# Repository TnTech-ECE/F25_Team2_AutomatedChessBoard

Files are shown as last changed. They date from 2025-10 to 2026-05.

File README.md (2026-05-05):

# Chess 2 Impress

## Executive Summary

Smart chessboards enhance the over-the-board chess experience through automated piece movement and AI opponent integration. Existing commercial options, however, cost hundreds to thousands of dollars (putting them out of reach for most players). Chess 2 Impress is a low-cost, accessible, **voice-controlled** chessboard (built for under $660 in materials). Players speak their moves using natural chess notation, and the board physically moves the pieces (using a CoreXY gantry with an under-board electromagnet). The system supports single-player games against the Stockfish chess engine, two-player games, and includes automated capture handling and board reset. Voice recognition runs locally on a Raspberry Pi (using the Vosk engine), requiring no internet connection. An LCD display provides real-time game feedback, and a battery-backed UPS allows over 2 hours of portable gameplay. The project demonstrates that a fully functional automated chess board can be built with off-the-shelf components (at less than commercial prices), while maintaining accessibility for players with limited mobility or visual impairments.

## Capabilities

- **Voice-controlled gameplay** using the Vosk speech recognition engine, supporting algebraic notation and common variations (e.g., "move knight a six," "move c2c4," "move castle"). There was a 97% first-try recognition accuracy across multiple speakers.
- **Automated piece movement** via a CoreXY gantry system driven by two NEMA 17 stepper motors and TMC2209 drivers, with an under-board electromagnet for contactless piece manipulation.
- **Edge-lane pathing algorithm** that routes pieces along square boundaries during movement, avoiding collisions with adjacent pieces on the board.
- **AI opponent integration** using the Stockfish chess engine for single-player games, with full move validation (through python-chess). This ensures 100% correct legal/illegal move classification.
- **Capture and reset handling** where captured pieces are automatically moved to dedicated discard rows, and the board resets all pieces to starting positions at the end of a game.
- **Binary UART communication** between the Raspberry Pi (processing) and Arduino Nano (motion control), with a handshake protocol that rejects boot noise and ensures reliable command transfer.
- **Battery-powered portable operation** via a DFRobot UPS HAT with 4×18650 cells, delivering over 2 hours of continuous gameplay (with seamless switchover from wall power).
- **LCD display feedback** showing move confirmations, illegal move alerts, game status, and system messages within approximately 1 second of voice input.
- **Fault protection** including TMC2209 DIAG pin monitoring, MOSFET flyback diode clamping, software position clamping (to prevent rail collisions), and EEPROM position saving.

## Salient Outcomes

- **Voice recognition exceeded expectations**: achieving 97% first-try recognition and 95% correctness (across 5 speakers with varied accents). This was well above the 80% specification.
- **The edge-lane pathing algorithm** was one of the most complex and iterative parts of the firmware development. Pieces must travel along square edges (never through intermediate square centres) to avoid displacing adjacent pieces. The final algorithm handles straight, diagonal, knight, and arbitrary L-shaped moves (for captures and discards) using a unified exit-edge / entry-edge framework.
- **Electromagnet switching latency measured at 3 microseconds**: over 3,300 times faster than the 10ms specification, demonstrating that the MOSFET circuit adds essentially zero delay to the move-completion budget.
- **The blown fuse debugging saga** taught the team that hardware failures can mimic software bugs. Multiple debugging sessions chasing "wrong direction" firmware issues were ultimately caused by a single blown fuse disabling one stepper motor, producing diagonal movement instead of the intended axis-aligned motion.
- **Move completion time remains the primary unmet specification**: Even the shortest possible move takes over 5 seconds with current firmware settings, and worst-case moves approach 30 seconds. Increasing stepper speed and acceleration in firmware is the straightforward fix, but could not be implemented without drastic redesigns to the electromagnet and acryllic setup.

## Project Demonstration & Images

**Demo Video:** (click the thumbnail below) Watch the video (https://youtu.be/9_9py33vPpE?si=CPKPgexxfqgLKRPD)

**Project Images:**

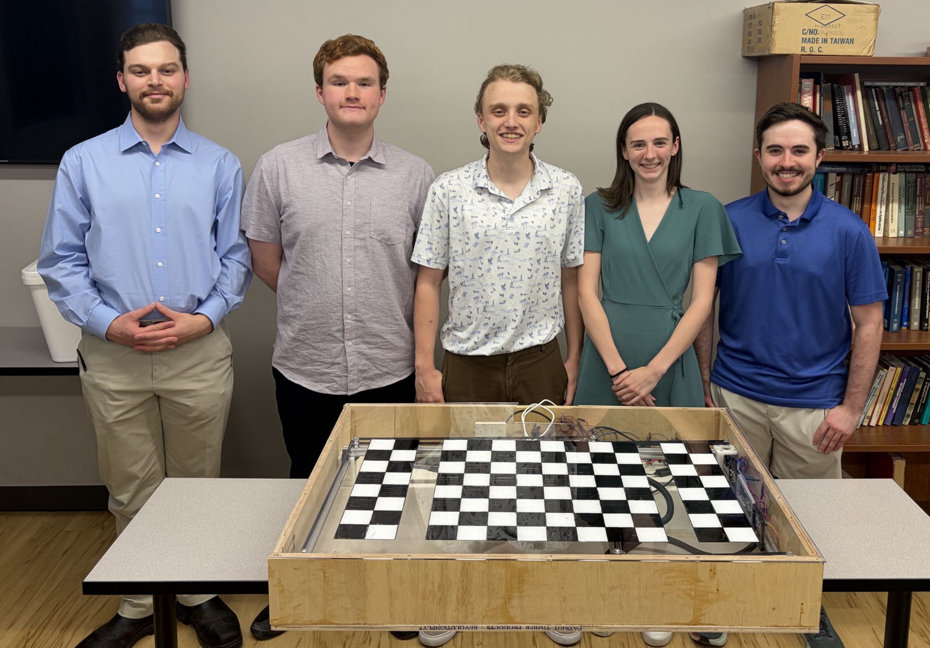
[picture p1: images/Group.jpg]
Group Photo


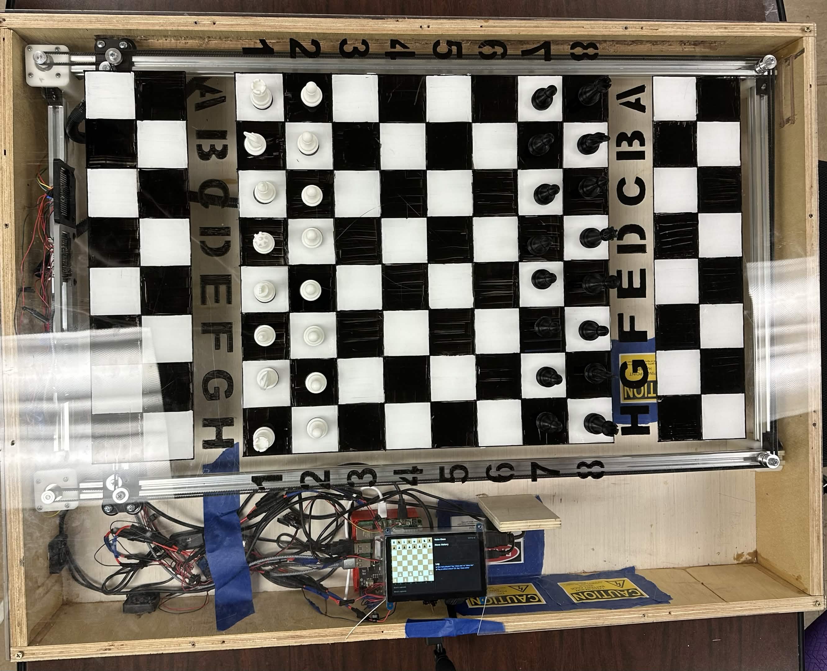
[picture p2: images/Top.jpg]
Top View


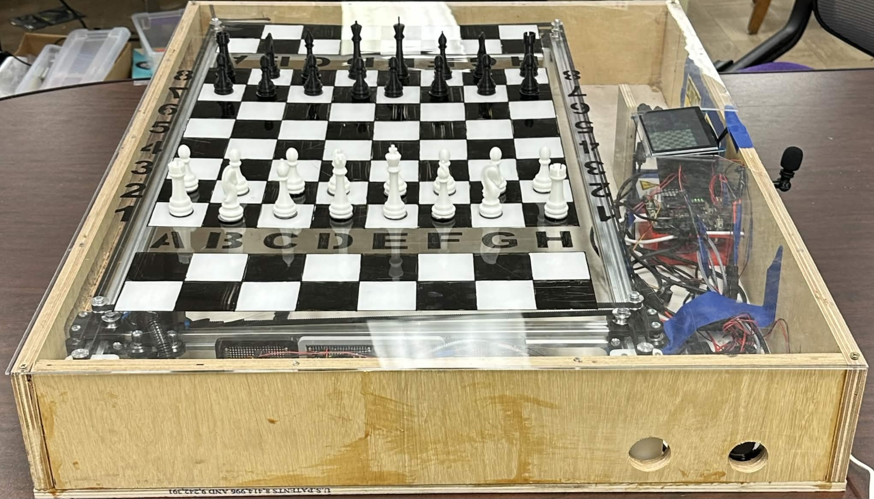
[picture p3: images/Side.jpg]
Side View


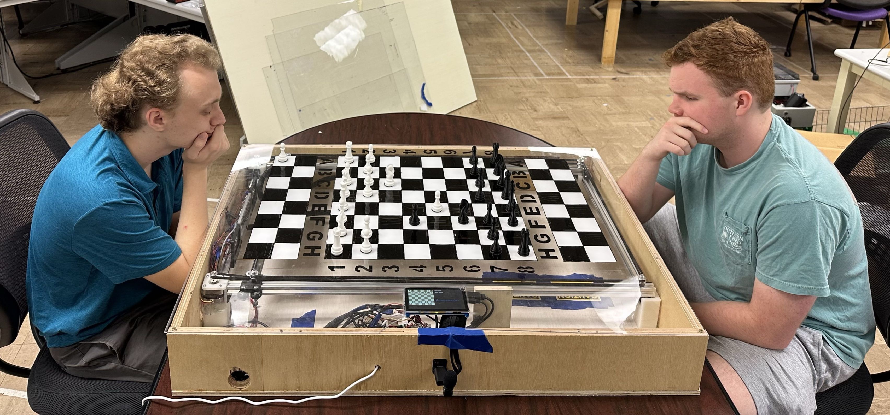
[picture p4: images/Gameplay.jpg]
Gameplay Example


## About Us

### Team

- **Nathan MacPherson** (Team Leader): Designed and integrated the Peripherals Unit, including the USB microphone interface and LCD display. Managed team coordination, designed the portability and weight experiments, and maintained the component inventory.
- **Noah Beaty** (Recorder): Developed the Control Unit firmware on the Arduino Nano, including the CoreXY motion engine, edge-lane pathing algorithm, binary UART protocol, electromagnet control, and fault protection. Designed the motion, electromagnet, flyback, command latency, and edge boundary experiments.
- **Jack Tolleson** (Treasurer): Built the Processing Unit on the Raspberry Pi, implementing the Vosk speech recognition pipeline, python-chess move validation, Stockfish AI integration, and UART communication with the Arduino. Designed the voice recognition, processing latency, and move validation experiments.
- **Allison Givens**: Designed and built the CoreXY mechanical subsystem, including the aluminum extrusion frame, belt/pulley system, the 3D-printed carriage, and the trolley supports. Iterated through numerous mechanical revisions to accommodate enclosure constraints. Designed the safety compliance experiment.
- **Lewis Bates**: Designed and built the Power Unit, including the DFRobot UPS HAT integration, 4×18650 battery pack, MT3608 boost converters, fuse protection, and power distribution. Designed power-related experiments (UPS switchover, sleep-mode draw, battery runtime, voltage regulation, and power budget verification).

### Faculty Supervisor

**Dr. Charles Van Neste**: Faculty advisor for the project.

### Stakeholders

The primary customer for this project is the **Tennessee Tech Chess Club**, represented by club president Max Bottoms. The club expressed interest in an affordable automated board that could be used for club events, demonstrations, and accessible play. Beyond the chess club, the project targets chess enthusiasts, hobbyists interested in replicating the build, and players with limited mobility or visual impairments (who benefit from voice-controlled, hands-free gameplay).

### Recognitions

Special thanks to our capstone instructor Dr. Christopher Storm Johnson, Julie Mountain, Sara Vandermyde, Jeff Randolph, the Tennessee Tech Chess Club, and our respective families for their support throughout the project.

## Repo Organization

### [Reports](./Reports)

Contains all project reports, including the Conceptual Design, Detailed Design documents, Experimental Analysis, project poster, and related supporting materials.

### [Documentation](./Documentation)

Contains project documentation including signoff sheets, meeting notes, the project datasheet, and design reference materials.

### [Software](./Software)

Contains all project source code organized by subsystem, including the Arduino Control Unit firmware (`chess_corexy.ino`), the Raspberry Pi Processing Unit code, and associated README files with installation and usage instructions.

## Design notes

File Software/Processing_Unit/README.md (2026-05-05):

# Voice Chess — Physical Board Controller

A voice-controlled chess system running on a Raspberry Pi 5. The player speaks moves aloud, the Pi validates them using python-chess. A Pygame display shows the board state, move history, and status messages in real time.

---

## What the Software Does

The system runs three concurrent threads:

- **Audio capture** — streams raw PCM audio from a USB microphone into a queue
- **Speech recognition** — Vosk processes audio chunks and recognises spoken chess commands
- **Game loop** — validates moves, runs Stockfish AI, and coordinates the physical board

Supported features:
- Voice move input using coordinate notation (`move e two e four`) or standard algebraic notation (`move knight f three`, `move e takes d five`)
- 1-player mode against Stockfish AI (Elo 1350) or 2-player local mode
- Physical piece movement via UART binary protocol to Arduino coreXY system
- Captured piece tracking with automatic capture zone management
- Castling, en passant, and promotion with physical piece swap
- Automatic board reset at end of each game using greedy Manhattan distance algorithm
- Draw detection (threefold repetition, fifty-move rule, stalemate, insufficient material)
- Pygame display showing board, move history, captured pieces, and message log
- Vosk watchdog that automatically recovers from speech recognition freezes

---

## Dependencies

### Hardware
- Raspberry Pi 5
- USB microphone
- Arduino Nano
- BSS138 logic level shifter (3.3V ↔ 5V)
- HDMI display (800×480 minimum)

### Operating System
- Raspberry Pi OS 
- PulseAudio running 
- Hardware UART enabled 

### Python Version
- Python 3.11 or later

### Python Packages
```
vosk
sounddevice
chess
pygame
pyserial
```

Install all at once:
```bash
pip install vosk sounddevice chess pygame pyserial --break-system-packages
```

### External Programs

### Vosk Model
- `vosk-model-small-en-us-0.15` — small English model, fast enough for real-time on Pi 5

Download from [https://alphacephei.com/vosk/models](https://alphacephei.com/vosk/models) and extract to the project directory.

## How to Install

**1. Clone or copy the project files to the Pi:**
```
chessproject/
├── chess_voice.py
├── piece_tracker.py
├── display.py
└── vosk-model-small-en-us-0.15/
```

**2. Create and activate a Python virtual environment:**
```bash
python3 -m venv chessenv
source chessenv/bin/activate
```

**3. Install Python dependencies inside the virtual environment:**
```bash
pip install vosk sounddevice chess pygame pyserial
```

**4. Install Stockfish:**

```bash
sudo apt install stockfish
```

Or install via snap:
```bash
sudo snap install stockfish
```

Verify it installed correctly:
```bash
which stockfish
/usr/games/stockfish
```

If stockfish is installed to a different path, update this line in `chess_voice.py`:
```python
engine = chess.engine.SimpleEngine.popen_uci("/usr/games/stockfish")
```

**5. Enable hardware UART on the Pi:**
```bash
sudo raspi-config
# Interface Options → Serial Port
# Login shell over serial: No
# Serial port hardware: Yes
```

**6. Allow shutdown without password** (required for "chess no" voice command):
```bash
sudo visudo
# Add this line:
server ALL=(ALL) NOPASSWD: /usr/sbin/shutdown
```

**7. (Optional) Set up autostart on boot:**

Create `/home/server/.config/autostart/chess.desktop`:
```ini
[Desktop Entry]
Type=Application
Name=Chess
Exec=bash -c 'cd /home/server/chessproject && source /home/server/chessenv/bin/activate && python3 chess_voice.py >> chess.log 2>&1'
```

---

## How to Run / How to Use

**Start the program:**
```bash
cd ~/chessproject
source ~/chessenv/bin/activate
python3 chess_voice.py
```

The program will wait for PulseAudio and the microphone to be ready before starting.

---

### Voice Commands

All commands require a wake word — either `move` for chess moves or `chess` for system commands.

**Setup commands:**
| Say | Action |
|---|---|
| `chess one` | 1-player mode vs Stockfish |
| `chess two` | 2-player mode |
| `chess white` | Play as white |
| `chess black` | Play as black |
| `chess yes` | Play again |
| `chess no` | Shut down |

**Move commands (coordinate notation):**
| Say | Example |
|---|---|
| `move [src] [dst]` | `move e two e four` |

**Move commands (algebraic notation):**
| Say | Example |
|---|---|
| Pawn to square | `move e four` |
| Piece to square | `move knight f three` |
| With "to" | `move knight to f three` |
| Pawn capture | `move e takes d five` |
| Piece capture | `move knight takes f three` |
| Disambiguated | `move rook a d one` |

**Special moves:**
| Say | Action |
|---|---|
| `move castle` | Castle (auto-detects side if only one available) |
| `move short` | Kingside castle |
| `move long` | Queenside castle |

**Promotion** — when a pawn reaches the back rank a menu appears automatically. Say:
```
move queen / move rook / move bishop / move knight
```
Only pieces the opponent has captured are available for promotion.

**Game commands:**
| Say | Action |
|---|---|
| `chess resign` | Resign — board resets immediately |

---

### Configuration

At the top of `chess_voice.py`:

```python
ARDUINO_CONNECTED = True   # False for testing without hardware (short ACK timeout)
```

At the top of `piece_tracker.py`:

```python
ack_timeout = 30.0   # seconds to wait for Arduino ACK per packet
```

In `chess_voice.py` recognition thread:

```python
WATCHDOG_TIMEOUT = 15.0   # seconds before Vosk is automatically reset
```

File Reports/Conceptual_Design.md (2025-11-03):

# Conceptual Design - Chess 2 Impress

## Introduction

Chess is a complex and strategic game that allows players to compete against each other on an even playing field with no hidden information. 
As it has grown more popular, new ways to enjoy this age old game have been developed. One of the most interesting examples of this is the automated chess board.
Automated chess boards are able to improve the user experience by changing the way that they interact with over the board chess. 
Vocal input is often used, making the board more accessible to people with a reduced range of motion while also being a fresh and new way to play.
These chess boards must also be able to move pieces around the board on their own, allowing users to compete against a computer and even other opponents online.
Although automated chess enhances over the board play, it is inaccessible to most due to its high price point. 

The demand for a cheaper option that does not compromise on functionality is clear. The proposed project aims to create a chess board that reliably recognizes voice input, automates piece movement, and integrates with computer opponents, all while continuing to be affordable.
The primary objective of this board is to bring the benefits that come with automated chess to a wider audience.

The conceptual design document will:
- Outline and define constraints to ensure that it is functional, reliable, and affordable.
- Examine potential solutions, comparing them and determining the best approach to meet the project's goals.
- Present a high level solution, detailing the board's internal architecture as well as its operational flow.
- Specify the details of individual subsystems.
- Address the standards the project must adhere to, as well as ethical and professional specifications.

## Fully Formulated Problem

The primary objective of this project is to design and build a low-cost, accessible, and intelligent automated chess board that enhances the traditional over-the-board (OTB) chess experience by integrating online play, AI-based solo play, and voice command functionality. The system shall support physical gameplay while interfacing with online platforms and allow players with physical or visual disabilities to engage in independent play through voice control and automated piece movement.

The system shall be constructed using affordable and readily available components to ensure replicability by hobbyists. In doing so, the board shall bridge the gap between digital and physical chess play while improving accessibility and reducing cost barriers.

### Specifications

The chessboard will meet the following requirements to ensure reliability and operability:

1. Vocal Processing System: The system shall enable players to control gameplay using spoken commands. 

    - Microphone (Peripheral Input): The device shall capture vocal output from users and transmit it to the processing unit for analysis.
    - Processing Unit: The unit shall utilize Vosk to process and filter voice input with a minimum accuracy of 80%. It shall listen for input only while a designated button is pressed or after a command word is detected, recognize commands in algebraic chess notation and common variations (e.g., “Knight to e5,” “Bishop a4”), and process commands within 5 seconds of button release or the end of voice input.
2. Piece Positioning XY Frame: The system shall magnetically drag pieces to the proper square using stepper motors to position pieces based on their x and y coordinates.
    - Processing Unit: The unit shall utilize Stockfish to enable single-player gameplay against an AI opponent.
    - Control Unit: The unit shall use an Arduino with Big Easy Drivers to interpret vocal commands, drive the XY movement, complete any piece movement within 5 seconds, and remove 95% of captured pieces without collision.
    - Core XY: The unit shall precisely position the magnetic actuator to relocate pieces while ensuring all pieces remain upright and stable during movement.

3. Visual Output: The system shall output game data to optimize user experience.
    - Display Screen (Peripheral Output): The device shall display move confirmations, illegal move alerts, and overall game status updates within 1 second of command processing. It shall display characters ≥ 10 pt for readability and support high-contrast text or graphics for clear visibility under standard indoor lighting.
4. Board Assembly: The system shall be assembled to minimize overall weight, support ease of transport, and improve user accessibility. The board shall weigh less than 30 pounds to allow transport by a single user and include features that facilitate transportability. File and rank labels shall be clearly displayed to assist users in locating squares during gameplay.
5. Power Supply System: The board shall include a sleep mode to reduce power consumption when idle and shall operate using rechargeable battery capable of supporting at least 2 hours of active gameplay.
6. System Design and Modularity: The final board shall cost no more than $350 USD in materials and have a modular design allowing for individual upgrades.

These specifications were developed in collaboration with stakeholders to define the system’s ideal functions while minimizing cost. They are designed to meet the functional requirements effectively, comply with relevant industry standards and regulations, and prioritize accessibility and user inclusion—all without compromising affordability or overall system performance.

### Constraints
- Regulatory and Compliance Constraints: To ensure the system meets U.S. consumer electronics and electrical standards.
    - Shall comply with FCC Part 15 Subpart B (Class B) limits for electromagnetic interference (EMI) in residential environments, which specify maximum conducted emissions of up to 0.15–30 MHz at 66–56 dBµV, decreasing with frequency, and radiated emissions of up to 30–1000 MHz at 40–54 dBµV/m measured at 3 meters. [1]  
    - Shall operate below 50 V DC, following UL low-voltage safety thresholds for maximum hazardous touch voltage to eliminate the need for high-voltage insulation. [2]  
    - Shall meet the requirements of NEC, NFPA 70 for low-voltage indoor consumer systems, which defines low-voltage circuits as those operating at 50 V or less and requires compliance with wiring methods specified in Article 725 for Class 1, 2, and 3 circuits, including protection against overcurrent, proper conductor sizing, and insulation rated for the circuit’s voltage. [3] 
    - Shall avoid use of materials or configurations that violate CPSC safety guidance for consumer electronics, including specification of materials with hazardous chemical content (e.g., lead, phthalates) or components lacking documented compliance with CPSC’s best-practice manufacturing guidance and material-change-testing requirements. [4]
    - Shall operate within the safe limits defined by UL 2054 for household and commercial batteries, ensuring that under normal use and foreseeable abuse conditions the battery does not exceed 302°F, remains between 32-140°F while charging, remains between -4–140 °F while discharging, does not catch fire or explode, and is protected against overcharge, short-circuit, mechanical abuse (crush, impact, vibration), and thermal extremes. [5]
- Electrical and Safety Constraints: To prevent electrical, thermal, and physical hazards during operation.
    - Shall limit external surface temperatures to ≤104 °F (40 °C) during continuous operation, in accordance with UL 94 flammability requirements for plastic materials and the CPSC maximum surface temperature guidelines (16 CFR 1505.7) to prevent thermal hazards. [6] [7]
    - Shall use cord sets, flexible cables, and connectors compliant with NEC Article 400, ensuring cords are rated for the system’s voltage and current and provide appropriate insulation and temperature rating, are routed to avoid sharp edges, pinch points, or areas of high foot traffic, with bends maintained above the minimum bend radius, connectors provide proper grounding continuity and are rated for the system’s operating voltage and current, and are secured using clips, cable trays, or protective raceways to minimize tripping hazards and mechanical damage. [8]
    - Shall include grounding, bonding, and electrical protection measures in accordance with OSHA 29 CFR 1910 Subpart S to minimize electrical shock hazards, ensuring all exposed conductive parts are properly grounded and circuit protection devices are installed where required [9].
    - Shall include ANSI Z535.4-compliant safety labels for all user-facing hazards, including moving parts, power indicators, and other electrical or mechanical hazards, ensuring labels are legible, durable, and placed conspicuously to effectively warn users of potential risks. [10]  
- Accessibility and Ergonomic Constraints: To ensure usability for a wide range of users.
    - Shall conform to Section 508 of the Rehabilitation Act, ensuring that all user interfaces, controls, and displays are accessible to individuals with disabilities, including compatibility with assistive technologies such as screen readers and alternative input devices. [11]
    - Shall follow ANSI/HFES 100‑2007 ergonomic guidelines, ensuring that controls and displays are positioned for comfortable reach, appropriate viewing angles, and clear tactile, visual, or auditory feedback to reduce operator fatigue and errors. [12] 
    - Shall apply universal design principles, minimizing cognitive and physical barriers by providing intuitive operation, clear labeling, and adjustable settings where feasible to accommodate a wide range of users. [13]

## Comparative Analysis of Potential Solutions

Automated chessboards have emerged as innovative tools for enhancing gameplay, integrating automation and dynamic AI opponents. Below, we analyze multiple subsystem solutions to determine their suitability for addressing the challenges of affordability, automated capabilities, and accessibility.

### Chess Piece Movement

_**Robotic Arm Manipulator System**_ [14]

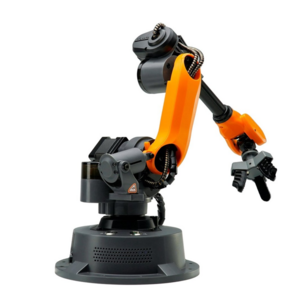
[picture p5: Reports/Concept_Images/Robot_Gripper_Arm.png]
Robotic Arm


The robotic arm manipulator system consists of a multi-jointed mechanical arm mounted above the chessboard, equipped with a claw or gripper to pick up and move chess pieces between positions. Controlled by servo or stepper motors, this approach mimics human motion, offering precise vertical and horizontal control for piece manipulation.

  * _Pros:_
  
    * Provides full 3D control and can directly lift pieces instead of sliding them.
    
    * Capable of handling a wide range of object shapes and sizes with a properly designed gripper.
    
    * Visually engaging and intuitive to observers due to its human-like movement.
    
    * Modular and programmable for other potential tasks or demonstrations.

  * _Cons:_
    
    * Mechanically complex with multiple degrees of freedom requiring advanced kinematic control.
    
    * Requires precise calibration to avoid collisions with other pieces or the board.
    
    * Considerably slower than planar motion systems.
    
    * Bulky structure obstructs the player's view.
    
    * Increased cost and mechanical wear due to multiple servos or stepper motors.
    
    * Noise and vibration from multiple moving joints can degrade precision.
    
    * Requires a robust frame or enclosure to maintain stability and alignment.

_**Individual Micro-Robot System**_ [15]

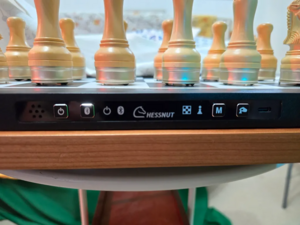
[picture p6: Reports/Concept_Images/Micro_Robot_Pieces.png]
Micro Robotics


This system places a small, self-contained micro-robot beneath each chess piece. Each robot can move independently under the board, guided by sensors or wireless communication, to reposition its corresponding piece as commanded. This concept is similar to systems used in high-end commercial robotic chessboards (such as the Chessnut Move[16]).

  * _Pros:_
  
    * Allows completely independent movement of each chess piece.
    
    * Eliminates the need for moving gantries, belts, or overhead mechanisms.
    
    * Offers smooth and realistic piece motion directly from below the board.

  * _Cons:_
    
    * Extremely expensive and complex to implement, requiring many individual actuators.
    
    * Difficult to synchronize multiple robots for coordinated movement.
    
    * Maintenance is cumbersome: each unit must be powered, calibrated, and serviced individually.
    
    * Requires precise alignment with chessboard grid and consistent magnetic coupling.
    
    * Limited battery life and power management challenges under a closed board.
    
    * Communication interference or loss can result in desynchronized or failed moves.

_**CoreXY Motion System**_ [17]

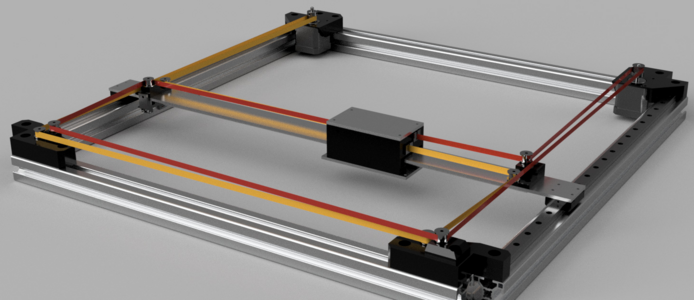
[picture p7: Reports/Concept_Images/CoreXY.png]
CoreXY Two-Axis


The CoreXY motion system uses two stepper motors connected through a pair of pulley and belt assemblies to enable precise, planar motion along the X and Y axes. A magnet is mounted to the movable head, allowing the system to position and actuate magnetic pieces from below the chessboard. This design provides a compact, fast, and mechanically efficient method for two-dimensional positioning, without requiring independent motorized axes.
  
  * _Pros:_
  
    * Provides high-speed, precise planar movement using only two motors.
    
    * Lightweight and mechanically efficient due to stationary motors and crossed belt layout.
    
    * Compatible with a wide range of stepper drivers.
    
    * Smooth, coordinated motion reduces mechanical vibration and improves accuracy.
  
  * _Cons:_
    
    * Requires careful calibration to prevent skewed or uneven motion.
    
    * Mechanical backlash or belt stretch can reduce repeatability over time.
    
    * Limited Z-axis functionality unless supplemented by another mechanism.
    
    * Performance depends on magnet strength and carriage rigidity for consistent actuation.

**Evaluation and Selection**

| | **Robotic Arm Manipulator** | **Individual Micro-Robot System** | **CoreXY Motion System** |
|:--|:--|:--|:--|
| **Mechanical Complexity** | High: multiple joints and servos | High: dozens of independent robots | Low: simple two-motor planar motion |
| **Precision and Accuracy** | Medium: depends on calibration | High: direct piece control | High: smooth and consistent positioning |
| **Speed of Operation** | Low: slow due to arm motion | Medium: piece-by-piece movement | High: fast planar translation |
| **Cost** | High: many actuators and materials | Very High: one robot per piece | Low: minimal motors and hardware |
| **Ease of Maintenance** | Low: mechanical wear and calibration | Very Low: each robot must be serviced | High: few components to maintain |
| **Scalability / Expandability** | Medium: modular but bulky | Low: limited by robot count and battery | High: adaptable to larger boards |
| **Reliability** | Medium: prone to alignment drift | Low: multiple failure points | High: robust motion structure |
| **Aesthetic / User Experience** | High: visually engaging | Medium: hidden motion below board | Medium: minimalistic, functional |
| **Overall Suitability** | Acceptable but inefficient | Impractical and costly | Optimal balance of performance and simplicity |

When evaluating the three systems, several key factors were considered: mechanical complexity, cost, precision, scalability, and ease of maintenance. The robotic arm, while versatile, introduces high mechanical complexity, slower operation speeds, and increased cost due to multiple motors and linkages. The micro-robot system provides independent piece control but is prohibitively expensive, difficult to synchronize, and challenging to maintain.

The CoreXY motion system was determined to be the most balanced and practical approach. Its two-motor planar configuration minimizes mechanical components while maximizing precision and speed. It integrates smoothly with magnetic actuation methods, provides consistent and predictable motion, and offers an excellent trade-off between performance and design simplicity.

### Processing and Control Subsystem

_**Centralized Processing Unit**_ [18]

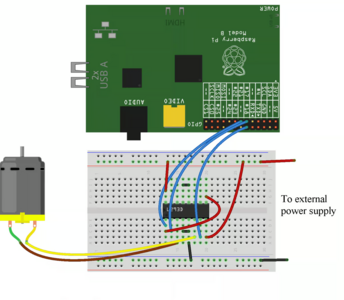
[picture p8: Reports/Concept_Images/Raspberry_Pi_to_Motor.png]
Centralized Processing Unit


In this setup, a single embedded processor (such as a Raspberry Pi) handles all major system functions, including speech recognition, chess logic, and motion control. The processor directly interfaces with motor driver boards, eliminating the need for a secondary control unit. This approach simplifies wiring and reduces communication overhead between devices, but places greater computational and timing demands on the processor.

  * _Pros:_
  
    * Simplified system architecture with fewer components and communication links.
    
    * Reduced latency and failure points, since all logic resides on one board.
    
    * Compact, space-efficient design requiring minimal wiring.
    
    * Suitable for small-scale prototypes or cost-sensitive builds.
  
  * _Cons:_
    
    * The single processor is not optimized for precise real-time control, potentially introducing motor timing inconsistencies.
    
    * Processor overload may occur when running several chess management programs and motion control tasks simultaneously.
    
    * A single hardware failure halts all system functionality.
    
    * Difficult to scale or maintain if additional sensors or actuators are later added.

_**Cloud-Assisted or Network-Based Processing**_ [19]

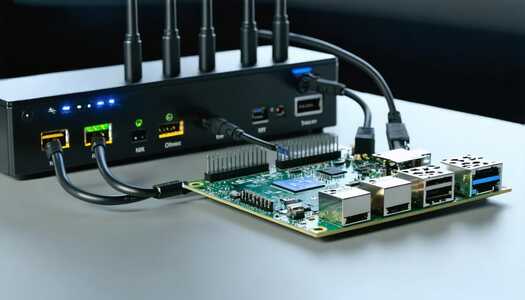
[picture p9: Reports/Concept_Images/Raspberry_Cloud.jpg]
Cloud Processing


In this configuration, the chessboard’s hardware handles only low-level control, while cloud or networked servers perform computationally heavy tasks such as speech recognition and chess AI. The local system sends input data (like voice or board state) to remote services, which return processed results. This approach leverages powerful external resources, but introduces significant dependency on network availability.

  * _Pros:_
  
    * Reduces on-board processing requirements, enabling smaller and lower-power hardware.
    
    * Allows use of advanced AI models beyond embedded capabilities.
    
    * Simplifies software maintenance through centralized, remotely updatable systems.
  
  * _Cons:_
    
    * Requires continuous internet connectivity, meaning the system is non-functional offline.
    
    * Introduces latency that can affect responsiveness in move execution and voice feedback.
    
    * Raises data security and privacy concerns.
    
    * Dependent on third-party APIs or services that may change or become unavailable.
    
    * Reduces autonomy and portability, making it unsuitable for standalone operation.

_**Distributed Processing and Control System**_ [20]

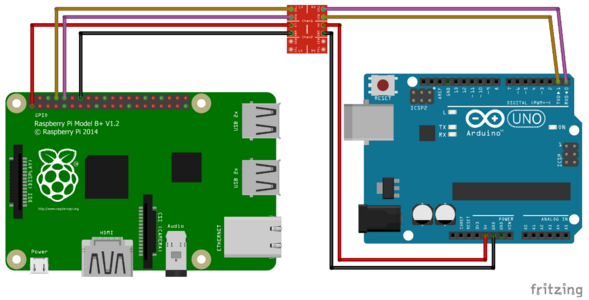
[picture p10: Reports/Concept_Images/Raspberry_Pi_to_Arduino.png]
Distributed Processing


This architecture separates high-level processing from real-time motor control. A Raspberry Pi acts as the main processing unit, running the voice recognition and chess piece tracking programs. It communicates with a dedicated Arduino control unit, which manages the CoreXY stepper motors through two motor driver boards. The Arduino executes time-critical control loops for precise movement, while the Raspberry Pi handles strategic computation and user interaction.

  * _Pros:_
  
    * Divides workload between two optimized processors, improving performance and reliability.
    
    * Provides smooth, accurate motion via the Arduino’s real-time control capabilities.
    
    * Enhances modularity, wherer each subsystem can be tested, replaced, or upgraded independently.
    
    * Allows the Raspberry Pi to focus on higher-level logic and communication, without timing interruptions.
    
    * Supports future expansion with minimal redesign.
  
  * _Cons:_
    
    * Requires careful synchronization between Pi and Arduino via serial or I²C communication.
    
    * Slightly higher cost and wiring complexity.
    
    * Debugging inter-device communication can be more challenging.
    
    * Adds a small latency overhead in transmitting commands between processors.

**Evaluation and Selection**

| | **Centralized Processing Unit** | **Cloud-Assisted Processing** | **Distributed Processing and Control System** |
|:--|:--|:--|:--|
| **Processing Performance** | Medium: single processor handles all tasks | Very High: uses powerful remote servers | High: tasks divided between Pi and Arduino |
| **Real-Time Control** | Low: limited motor timing precision | Very Low: dependent on network latency | High: Arduino provides dedicated control loop |
| **System Reliability** | Medium: single-point failure risk | Low: relies on external network and servers | High: separate units improve fault tolerance |
| **Offline Functionality** | High: operates fully offline | Very Low: requires continuous internet | High: fully self-contained system |
| **Scalability / Expandability** | Medium: limited by single processor | Medium: scalable through cloud resources | High: modular and easily extendable design |
| **Latency and Responsiveness** | High: direct control, minimal communication delay | Low: network delay affects interaction | High: responsive with minimal inter-device delay |
| **Maintenance and Debugging** | High: single board simplifies updates | Medium: dependent on external software updates | Medium: slightly complex multi-device debugging |
| **Hardware Cost** | Low: only one main board needed | Medium: requires network hardware or subscription | Medium: two controllers and wiring required |
| **Data Security and Privacy** | High: all processing local | Low: sensitive data passes through cloud | High: secure local processing and control |
| **Overall Suitability** | Acceptable for simple systems | Poor for standalone real-time control | Excellent balance of performance and reliability |

For this project, we prioritized reliable offline performance, precise motion control, and efficient processing distribution. The centralized processing system, while simple, risks performance bottlenecks when running both AI and motor control on one processor, and a single failure would disable the entire board. The cloud-assisted approach, although powerful, depends on constant internet connectivity and introduces latency, making it unreliable for real-time, portable use.

The Distributed Processing and Control System offers the best balance between responsiveness, modularity, and performance. By assigning real-time motion control to the Arduino and high-level processing to the Raspberry Pi, the system maintains smooth CoreXY operation (while supporting advanced features like voice recognition and chess logic). This design ensures scalability, reliability, and consistent offline operation, meeting all project goals effectively.

### Power System

_**Corded Power System**_ [21]

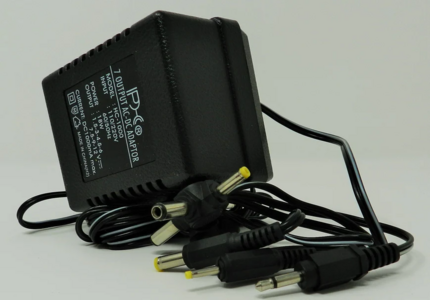
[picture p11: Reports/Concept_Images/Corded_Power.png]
Corded Power


The corded power configuration supplies energy directly from a wall outlet through a DC power adapter, providing continuous and stable voltage to all internal components. This setup eliminates the need for internal energy storage and simplifies circuit design, relying entirely on an external power connection for operation.

  * _Pros:_
  
    * Provides stable, uninterrupted power during operation.
    
    * Simplifies internal circuitry, with no need for charging or battery management systems.
    
    * Reduces weight by eliminating onboard batteries.
    
    * Inexpensive and straightforward to implement.
  
  * _Cons:_
    
    * Requires a constant connection to a wall outlet, limiting portability.
    
    * Operation is impossible without external power.
    
    * Increases cable clutter and reduces design aesthetics.
    
    * Potential tripping or cable strain hazards in user environments.
    
    * Less appealing for demonstration or mobile use cases due to lack of autonomy.

_**Wireless Inductive Power System**_ [22]

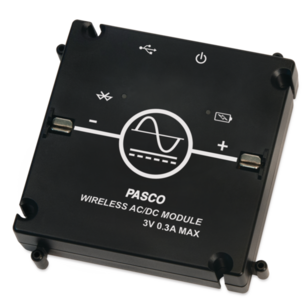
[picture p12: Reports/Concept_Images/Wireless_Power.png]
Wireless Power


A wireless inductive power setup transfers energy through magnetic coupling between a transmitter coil (in a base station) and a receiver coil integrated into the chessboard. This provides a cable-free appearance and continuous power when the board is positioned on its charging pad.

  * _Pros:_
  
    * Provides a modern, cable-free aesthetic for clean presentation.
    
    * Reduces wear on connectors from frequent plugging and unplugging.
    
    * Safe, low-voltage energy transfer suitable for consumer environments.
  
  * _Cons:_
    
    * Significantly lower power transfer efficiency.
    
    * Requires precise alignment between coils for consistent operation.
    
    * Limited power output, unsuitable for high-current loads like motors or magnets.
    
    * Increased system cost and design complexity.
    
    * Inefficient for continuous or high-load use, especially with moving actuators.
    
    * Thermal buildup during long operation could reduce component lifespan.
   
 _**Hybrid Power System**_ [23]

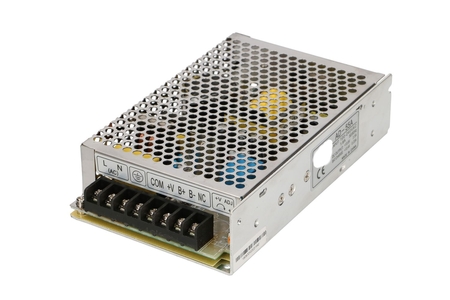
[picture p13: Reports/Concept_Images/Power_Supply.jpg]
Hybrid Power
 

The hybrid power system integrates a rechargeable battery pack with an AC adapter and power management circuitry. This configuration allows the chessboard to operate from wall power while simultaneously charging the batteries, and to continue functioning seamlessly on battery power when unplugged. It ensures both reliability and portability, making it ideal for extended demonstrations or classroom use.

  * _Pros:_
  
    * Enables uninterrupted operation whether plugged in or running on battery power.
    
    * Provides portability without sacrificing power availability.
    
    * Extends battery life through managed charging cycles and pass-through power.
    
    * Offers redundancy, where if one power source fails, the other maintains functionality.
    
    * Clean, professional design with minimal cable dependency.
    
  * _Cons:_
    
    * Slightly higher cost due to the inclusion of power management circuitry.
    
    * Requires careful design to balance charging and discharge loads.
    
    * Batteries will eventually require replacement after several hundred charge cycles.
    
    * Slightly heavier than a purely corded design.

**Evaluation and Selection**

| | **Corded Power System** | **Wireless Inductive Power System** | **Hybrid Power System** |
|:--|:--|:--|:--|
| **Power Reliability** | Very High: continuous stable voltage from wall outlet | Low: alignment and efficiency issues cause inconsistent delivery | Very High: reliable from wall or battery |
| **Efficiency** | High: minimal conversion loss with direct DC supply | Low: magnetic coupling losses reduce power transfer rate | Medium: conversion losses during charge and discharge |
| **Portability** | Very Low: requires constant outlet connection | Medium: limited to operation on charging pad | High: operates on battery or wall power |
| **System Complexity** | Low: no battery or management circuitry required | High: requires coil alignment and driver hardware | Medium: includes charge management and control circuits |
| **Cost** | Low: inexpensive and simple implementation | High: inductive components increase cost | Medium: additional circuitry and batteries add moderate cost |
| **Weight** | Low: no batteries required | Low: minimal internal hardware | Medium: includes rechargeable battery pack |
| **Safety** | Medium: tripping and strain hazards from cables | High: sealed, low-voltage energy transfer | High: regulated circuits and protected battery system |
| **Aesthetics** | Low: visible cords reduce visual appeal | Very High: clean, fully wireless appearance | High: minimal cables with clean overall design |
| **Suitability for Motors and Magnets** | Very High: provides stable, high-current supply | Very Low: limited power capacity for motor loads | Very High: supports actuator demands via wall or battery |
| **Overall Suitability** | Acceptable for stationary setups | Poor for high-load mobile operation | Excellent balance of flexibility, reliability, and performance |

When comparing the three power configurations, the hybrid system clearly offers the best balance of reliability, mobility, and functionality. The corded design, while simple and inexpensive, limits the system’s usability by requiring a constant power connection. The wireless inductive setup, although sleek, introduces inefficiency and insufficient power transfer for motor-driven systems.

The Hybrid Power System was therefore selected as the most practical and flexible option. It provides uninterrupted operation whether plugged in or on battery power, supports demonstrations and transportability, and ensures a professional, user-friendly design well-suited for the automated chessboard.

### Peripheral Subsystem

_**Button Input and LED Response System**_ [11^]

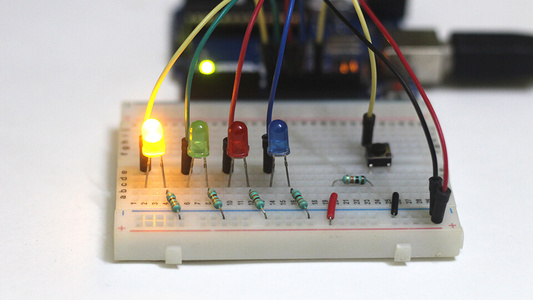
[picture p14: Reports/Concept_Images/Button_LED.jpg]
Buttons and LEDs output


In this configuration, user input is handled through a small set of physical buttons, while system feedback is provided by LEDs. Each LED color corresponds to specific system states, such as move confirmation and error detection. This design is simple and inexpensive, but less intuitive and less scalable for complex command sets.

  * _Pros:_
  
    * Extremely simple, durable, and low-cost hardware.
    
    * Provides immediate and reliable feedback without display lag.
    
    * Highly power efficient and resilient to environmental noise.
    
  * _Cons:_

    * Does not meet hands-free accessibility goals of the project.
    
    * Not suitable for complex communication or detailed error reporting.
    
    * Requires user memorization of LED meanings or tone patterns.

_**Microphone and Computer-Voice Response System**_ [12^]

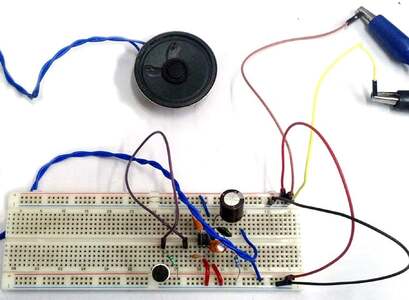
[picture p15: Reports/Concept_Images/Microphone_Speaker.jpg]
Microphone input and Speaker output


This option uses a microphone for user voice commands and a synthesized computer voice for system feedback. The system reads back recognized commands, requests confirmation, and communicates status or errors verbally. It eliminates the need for a screen, relying entirely on audio-based interaction. While fully hands-free, this setup depends heavily on clear audio input and output, which can be unreliable in noisy or shared environments.

  * _Pros:_
  
    * Fully hands-free operation enhances user convenience and accessibility.
    
    * Provides a more interactive and conversational user experience.
    
    * Reduces physical hardware needs by removing displays or buttons.
    
  * _Cons:_
    
    * Audio feedback can be difficult to hear or distinguish in noisy environments.
    
    * Lack of visual feedback may lead to miscommunication or missed confirmations.
    
    * Requires reliable speech synthesis and recognition performance.
    
    * Adds processing overhead and complexity to handle real-time voice interaction.

_**Microphone and LCD Display System**_ [24]

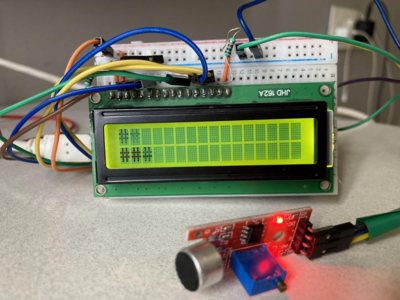
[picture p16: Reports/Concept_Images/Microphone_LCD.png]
Microphone input and LCD output


This setup integrates a microphone for voice command input and an LCD display for visual feedback. The user speaks a command (e.g., "move knight to F3"), which the system processes and displays on the screen for confirmation. The LCD also reports move confirmations, invalid commands, or mechanical errors detected during operation. The player can then issue a "confirm" or "cancel" voice command to finalize or reject the action. This configuration provides a balanced mix of hands-free control and clear, visual verification for reliable gameplay.

  * _Pros:_
  
    * Offers clear, readable feedback for every system action and voice command.
    
    * Enables confirmation and error display directly on the board, improving user confidence.
    
    * Hands-free operation through voice commands enhances accessibility and modern design appeal.
    
    * Allows debugging and system messages to be shown without external devices.
    
  * _Cons:_
    
    * Requires both voice recognition and display integration, slightly increasing hardware and coding complexity.
    
    * LCD may have limited viewing angles or space for longer messages.
    
    * Voice command errors may require multiple attempts in noisy environments.

**Evaluation and Selection**

| | **Button Input and LED Response System** | **Microphone and Computer-Voice Response System** | **Microphone and LCD Display System** |
|:--|:--|:--|:--|
| **Accessibility / Hands-Free Operation** | Very Low: requires manual interaction | Very High: fully voice-based operation | High: hands-free input with clear visual confirmation |
| **Communication Clarity** | Low: limited to color and tone cues | Medium: relies on clear audio input/output | Very High: clear text-based display feedback |
| **Error Handling / Feedback Detail** | Low: difficult to convey detailed error messages | Medium: audio feedback can miss details | High: LCD provides precise feedback and debugging info |
| **Environmental Reliability** | Very High: unaffected by noise or lighting | Low: performance drops in noisy environments | High: visual display unaffected by ambient sound |
| **Hardware Complexity** | Low: minimal components and wiring | Medium: requires microphone and speaker setup | Medium: integrates microphone and LCD circuitry |
| **Software Complexity** | Low: simple logic for LEDs and buttons | High: needs speech recognition and synthesis | Medium: speech recognition plus display interface |
| **Power Consumption** | Very Low: efficient LED operation | Medium: continuous audio I/O consumes more power | Medium: LCD backlight and voice processing use more power |
| **Cost** | Very Low: cheapest option | Medium: added cost for audio hardware | Medium: cost of LCD balanced by small component count |
| **User Experience** | Low: unintuitive and limited feedback | Medium: interactive but prone to voice errors | Very High: combines clarity, control, and accessibility |
| **Overall Suitability** | Acceptable for simple systems | Adequate for fully voice-based setups | Excellent balance of usability, feedback, and accessibility |

When evaluating the three interface approaches, key considerations included clarity of communication, accessibility, error handling, and ease of integration. The button and LED system, while simple and robust, cannot effectively convey complex messages or support conversational operation. The fully audio-based system offers modern appeal but lacks the reliability and clarity needed for precise chess move confirmations.

The Microphone and LCD Display System was selected as the most balanced and functional approach. It merges the hands-free convenience of voice input with the reliability of visual confirmation, allowing players to verify actions before execution. This hybrid interface supports clear communication, flexible debugging, and a polished user experience aligned with the chessboard’s intelligent design goals.

## High-Level Solution

The automated chess board integrates mechanical motion, artificial intelligence, and voice recognition into a unified platform that will enable users to play chess naturally through verbal commands. By coordinating the different sections of the chess board, the design achieves helpful communication, precise motion control, and user interaction. The accompanying block diagram illustrates how each subsystem contributes to the overall architecture through defined input-output relationships, such as power distribution and data flow. Meanwhile, the operational flowchart illustrates the sequence of system interactions, showing how changes in the chessboard’s state drive corresponding user inputs and system responses. This representation highlights the system’s flow, making sure of the communication between components while also minimizing latency, reducing processing overhead, and maintaining performance. Together, these design diagrams present a resource efficient solution that effectively balances system complexity, computational performance, and user experience.

### Hardware Block Diagram

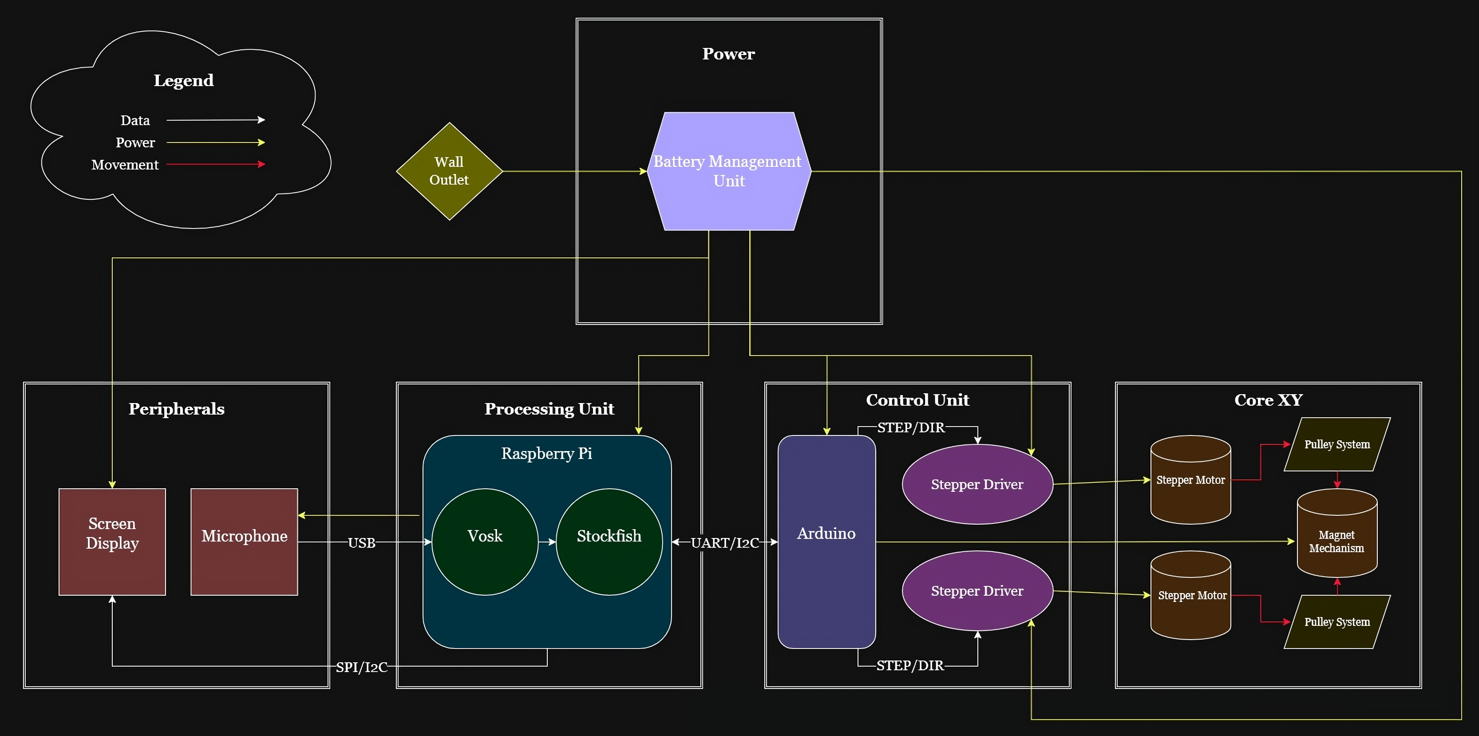
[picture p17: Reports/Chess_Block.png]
Block_Diagram


#### Processing Unit
The Processing Unit will consist of a Raspberry Pi responsible for coordinating all high-level system operations. Its primary functions are fourfold. First, it will interpret incoming audio signals from the microphone using the Vosk speech recognition engine to convert spoken commands into recognizable text, while also supplying power to the microphone. A USB interface was selected for the microphone connection due to the wide availability of inexpensive USB microphones and the Raspberry Pi’s native support for USB audio devices. Second, it will maintain the internal state of the chessboard and verify the legality of player moves using the Stockfish chess engine. Third, it will transmit validated and legal move commands to the Control Unit (Arduino) for conversion into motion control instructions. Communication between the Raspberry Pi and Arduino will occur via a USART or I²C connection, providing a reliable and simple serial data link between processors. Lastly, the Raspberry Pi will send display data to the screen, providing the user with real-time visual feedback on system activity and game status. The display will communicate with the Raspberry Pi using either the I²C or SPI protocol, chosen for their simplicity and compatibility with small embedded screens.
#### Control Unit
The Control Unit will oversee all motion control operations and act as the communication bridge between the Processing Unit and the mechanical subsystems. It will receive movement instructions from the Raspberry Pi, translate them into executable control signals for the CoreXY motors, and relay status or confirmation messages back to the Processing Unit. The Arduino will communicate with the stepper motor drivers using standard step and direction (STEP/DIR) signals, which are widely supported and allow for precise motor control. These functions will be facilitated by the Arduino, which will coordinate communication with the stepper motor drivers integrated within the Control Unit. Additionally, the Arduino may supply power to the magnetic mechanism, depending on the final design implementation.
#### Core XY Unit
The CoreXY Unit is responsible for executing all physical movements required to reposition chess pieces on the board. Upon receiving step and direction signals from the Control Unit, it operates two stepper motors that drive a system of belts and pulleys to move a magnetic carriage along the X and Y axes. The integrated magnetic mechanism enables the controlled relocation of individual chess pieces without disturbing adjacent pieces.
#### Peripherals Unit
The Peripherals Unit comprises the system’s input and output devices — the microphone and the display screen. The microphone captures user voice commands, potentially utilizing software-based noise filtering to enhance accuracy and clarity. The display provides visual feedback to the player, presenting system messages such as “Not a Legal Move” or “Pawn to A5,” along with overall game status updates. Both peripherals interface directly with the Raspberry Pi, receiving data and power as needed to support their respective software components. Together, these peripherals establish the user interface that enables effective interaction with the system.
#### Power Unit
The Power Unit supplies regulated electrical power to all other subsystems. It will consist of a battery-based power source designed to provide multiple voltage levels to meet the varying current and voltage requirements of each component. The 12V rail will supply power to the stepper motors and drivers, while the 5V rail will support the Raspberry Pi, Arduino, and other control and peripheral electronics. Proper power regulation and distribution are essential to ensure safe, stable, and efficient system operation.

### Operational Flow Chart

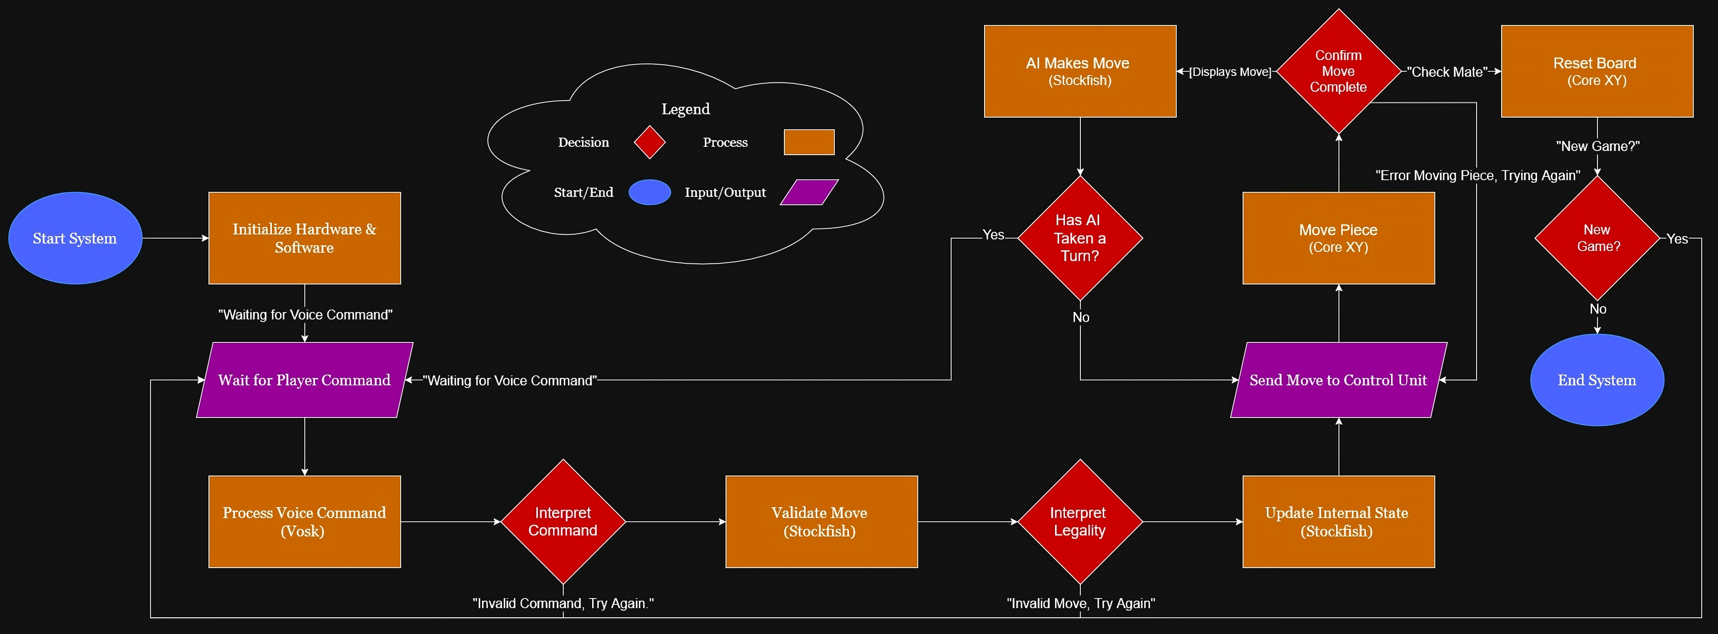
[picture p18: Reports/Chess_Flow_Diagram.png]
Block_Diagram


This diagram illustrates the overall operational flow of the automatic chessboard system, including both user interactions and the underlying processes required to generate the on-screen display. At startup, all hardware and software components initialize and configure their respective systems. Once initialization is complete, the display indicates that the board is ready for user input.

The user then provides a command, which the system processes to determine whether it represents a valid chess move. If the command is both recognized and legal, the system executes the move by physically repositioning the piece and updating the visual display to reflect the new board state.

Next, the opposing player (either the integrated AI engine or another human participant) takes a turn following the same sequence of validation, movement, and display update. This turn-based cycle continues until one player achieves checkmate. When the game concludes, the display presents the final result and the board automatically resets the pieces to their starting positions. Finally, the system prompts the user to decide whether to begin a new game.

### Key Features

1. Voice Controls
   - The microphone captures user commands upon a designated button press or voice command trigger.
   - The processing unit uses Vosk to process and filter voice commands, recognizing different accents and speech patterns.
2. Automated Piece Movement
   - The Arduino interprets processed voice commands and controls Big Easy Drivers to operate the stepper motors.
   - Stepper motors precisely drive the magnetic carriage to reposition chess pieces accurately on the board.
3. Visual Feedback
   - Display screen shows move confirmations, illegal move alerts, and game status.
   - Supports accessibility for players who may have hearing impairments or require additional visual cues.
4. User Accessibility
   - The system design emphasizes simplicity and intuitive use, minimizing the need for direct physical interaction.
   - Voice recognition supports a variety of player voices, including different accents and frequencies.
5. Power and Efficiency
   - The system includes an idle or sleep mode to conserve energy when not in active use.
   - The board provides at least 2 hours of continuous gameplay on battery power.
6. Modularity and Scalability
   - The design supports easy upgrades or replacements of individual subsystems by hobbyists or users.
   - Comprehensive documentation facilitates user modifications and future development.
7. Portability and Durability
   - The board is lightweight for easy transport and includes a carrying method for convenience.
   - The system is constructed from durable materials to prevent damage during normal use.
8. Cost Efficiency
   - The system is designed to remain under $350 USD in material costs while maintaining or exceeding the quality of comparable solutions.

### Relevant Constraints
#### Processing Unit Constraints: 
- Shall comply with FCC Part 15 Subpart B (Class B) limits for electromagnetic interference (EMI) in residential environments, which specify maximum conducted emissions of up to 0.15–30 MHz at 66–56 dBµV, decreasing with frequency, and radiated emissions of up to 30–1000 MHz at 40–54 dBµV/m measured at 3 meters. [1]
- Shall operate below 50 V DC, following UL low-voltage safety thresholds for maximum hazardous touch voltage to eliminate the need for high-voltage insulation. [2]  
- Shall meet the requirements of NEC, NFPA 70 for low-voltage indoor consumer systems, which defines low-voltage circuits as those operating at 50 V or less and requires compliance with wiring methods specified in Article 725 for Class 1, 2, and 3 circuits, including protection against overcurrent, proper conductor sizing, and insulation rated for the circuit’s voltage. [3]
- Shall avoid use of materials or configurations that violate CPSC safety guidance for consumer electronics, including specification of materials with hazardous chemical content (e.g., lead, phthalates) or components lacking documented compliance with CPSC’s best-practice manufacturing guidance and material-change-testing requirements. [4]
- Shall limit external surface temperatures to ≤104 °F (40 °C) during continuous operation, in accordance with UL 94 flammability requirements for plastic materials and the CPSC maximum surface temperature guidelines (16 CFR 1505.7) to prevent thermal hazards. [6] [7] 
- Shall use cord sets, flexible cables, and connectors compliant with NEC Article 400, ensuring cords are rated for the system’s voltage and current and provide appropriate insulation and temperature rating, are routed to avoid sharp edges, pinch points, or areas of high foot traffic, with bends maintained above the minimum bend radius, connectors provide proper grounding continuity and are rated for the system’s operating voltage and current, and are secured using clips, cable trays, or protective raceways to minimize tripping hazards and mechanical damage. [8]
- Shall include grounding, bonding, and electrical protection measures in accordance with OSHA 29 CFR 1910 Subpart S to minimize electrical shock hazards, ensuring all exposed conductive parts are properly grounded and circuit protection devices are installed where required. [9]
- Shall include ANSI Z535.4-compliant safety labels for all user-facing hazards, including moving parts, power indicators, and other electrical or mechanical hazards, ensuring labels are legible, durable, and placed conspicuously to effectively warn users of potential risks. [10] 

#### Control Unit Constraints: 
- Shall comply with FCC Part 15 Subpart B (Class B) limits for electromagnetic interference (EMI) in residential environments, which specify maximum conducted emissions of up to 0.15–30 MHz at 66–56 dBµV, decreasing with frequency, and radiated emissions of up to 30–1000 MHz at 40–54 dBµV/m measured at 3 meters. [1]
- Shall operate below 50 V DC, following UL low-voltage safety thresholds for maximum hazardous touch voltage to eliminate the need for high-voltage insulation. [2]  
- Shall meet the requirements of NEC, NFPA 70 for low-voltage indoor consumer systems, which defines low-voltage circuits as those operating at 50 V or less and requires compliance with wiring methods specified in Article 725 for Class 1, 2, and 3 circuits, including protection against overcurrent, proper conductor sizing, and insulation rated for the circuit’s voltage. [3]
- Shall avoid use of materials or configurations that violate CPSC safety guidance for consumer electronics, including specification of materials with hazardous chemical content (e.g., lead, phthalates) or components lacking documented compliance with CPSC’s best-practice manufacturing guidance and material-change-testing requirements. [4]
-  Shall limit external surface temperatures to ≤104 °F (40 °C) during continuous operation, in accordance with UL 94 flammability requirements for plastic materials and the CPSC maximum surface temperature guidelines (16 CFR 1505.7) to prevent thermal hazards. [6] [7]
- Shall use cord sets, flexible cables, and connectors compliant with NEC Article 400, ensuring cords are rated for the system’s voltage and current and provide appropriate insulation and temperature rating, are routed to avoid sharp edges, pinch points, or areas of high foot traffic, with bends maintained above the minimum bend radius, connectors provide proper grounding continuity and are rated for the system’s operating voltage and current, and are secured using clips, cable trays, or protective raceways to minimize tripping hazards and mechanical damage. [8]  
- Shall include grounding, bonding, and electrical protection measures in accordance with OSHA 29 CFR 1910 Subpart S to minimize electrical shock hazards, ensuring all exposed conductive parts are properly grounded and circuit protection devices are installed where required. [9]  
- Shall include ANSI Z535.4-compliant safety labels for all user-facing hazards, including moving parts, power indicators, and other electrical or mechanical hazards, ensuring labels are legible, durable, and placed conspicuously to effectively warn users of potential risks. [10]

#### Core XY Unit Constraints: 
- Shall comply with FCC Part 15 Subpart B (Class B) limits for electromagnetic interference (EMI) in residential environments, which specify maximum conducted emissions of up to 0.15–30 MHz at 66–56 dBµV, decreasing with frequency, and radiated emissions of up to 30–1000 MHz at 40–54 dBµV/m measured at 3 meters. [1] 
- Shall operate below 50 V DC, following UL low-voltage safety thresholds for maximum hazardous touch voltage to eliminate the need for high-voltage insulation. [2] 
- Shall meet the requirements of NEC, NFPA 70 for low-voltage indoor consumer systems, which defines low-voltage circuits as those operating at 50 V or less and requires compliance with wiring methods specified in Article 725 for Class 1, 2, and 3 circuits, including protection against overcurrent, proper conductor sizing, and insulation rated for the circuit’s voltage. [3]
- Shall avoid use of materials or configurations that violate CPSC safety guidance for consumer electronics, including specification of materials with hazardous chemical content (e.g., lead, phthalates) or components lacking documented compliance with CPSC’s best-practice manufacturing guidance and material-change-testing requirements. [4]
- Shall limit external surface temperatures to ≤104 °F (40 °C) during continuous operation, in accordance with UL 94 flammability requirements for plastic materials and the CPSC maximum surface temperature guidelines (16 CFR 1505.7) to prevent thermal hazards. [6] [7]  
- Shall use cord sets, flexible cables, and connectors compliant with NEC Article 400, ensuring cords are rated for the system’s voltage and current and provide appropriate insulation and temperature rating, are routed to avoid sharp edges, pinch points, or areas of high foot traffic, with bends maintained above the minimum bend radius, connectors provide proper grounding continuity and are rated for the system’s operating voltage and current, and are secured using clips, cable trays, or protective raceways to minimize tripping hazards and mechanical damage. [8] 
- Shall include grounding, bonding, and electrical protection measures in accordance with OSHA 29 CFR 1910 Subpart S to minimize electrical shock hazards, ensuring all exposed conductive parts are properly grounded and circuit protection devices are installed where required. [9] 
- Shall include ANSI Z535.4-compliant safety labels for all user-facing hazards, including moving parts, power indicators, and other electrical or mechanical hazards, ensuring labels are legible, durable, and placed conspicuously to effectively warn users of potential risks. [10] 

#### Peripherals Unit Constraints: 
- Shall comply with FCC Part 15 Subpart B (Class B) limits for electromagnetic interference (EMI) in residential environments, which specify maximum conducted emissions of up to 0.15–30 MHz at 66–56 dBµV, decreasing with frequency, and radiated emissions of up to 30–1000 MHz at 40–54 dBµV/m measured at 3 meters. [1]
- Shall operate below 50 V DC, following UL low-voltage safety thresholds for maximum hazardous touch voltage to eliminate the need for high-voltage insulation. [2]
- Shall meet the requirements of NEC, NFPA 70 for low-voltage indoor consumer systems, which defines low-voltage circuits as those operating at 50 V or less and requires compliance with wiring methods specified in Article 725 for Class 1, 2, and 3 circuits, including protection against overcurrent, proper conductor sizing, and insulation rated for the circuit’s voltage. [3]
- Shall avoid use of materials or configurations that violate CPSC safety guidance for consumer electronics, including specification of materials with hazardous chemical content (e.g., lead, phthalates) or components lacking documented compliance with CPSC’s best-practice manufacturing guidance and material-change-testing requirements. [4]
- Shall limit external surface temperatures to ≤104 °F (40 °C) during continuous operation, in accordance with UL 94 flammability requirements for plastic materials and the CPSC maximum surface temperature guidelines (16 CFR 1505.7) to prevent thermal hazards. [6] [7]
- Shall use cord sets, flexible cables, and connectors compliant with NEC Article 400, ensuring cords are rated for the system’s voltage and current and provide appropriate insulation and temperature rating, are routed to avoid sharp edges, pinch points, or areas of high foot traffic, with bends maintained above the minimum bend radius, connectors provide proper grounding continuity and are rated for the system’s operating voltage and current, and are secured using clips, cable trays, or protective raceways to minimize tripping hazards and mechanical damage. [8]  
- Shall include grounding, bonding, and electrical protection measures in accordance with OSHA 29 CFR 1910 Subpart S to minimize electrical shock hazards, ensuring all exposed conductive parts are properly grounded and circuit protection devices are installed where required [9]
- Shall conform to Section 508 of the Rehabilitation Act, ensuring that all user interfaces, controls, and displays are accessible to individuals with disabilities, including compatibility with assistive technologies such as screen readers and alternative input devices. [11]
- Shall follow ANSI/HFES 100‑2007 ergonomic guidelines, ensuring that controls and displays are positioned for comfortable reach, appropriate viewing angles, and clear tactile, visual, or auditory feedback to reduce operator fatigue and errors. [12] 
- Shall apply universal design principles, minimizing cognitive and physical barriers by providing intuitive operation, clear labeling, and adjustable settings where feasible to accommodate a wide range of users. [13] 

#### Power Unit Constraints: 
- Shall comply with FCC Part 15 Subpart B (Class B) limits for electromagnetic interference (EMI) in residential environments, which specify maximum conducted emissions of up to 0.15–30 MHz at 66–56 dBµV, decreasing with frequency, and radiated emissions of up to 30–1000 MHz at 40–54 dBµV/m measured at 3 meters. [1]
- Shall operate below 50 V DC, following UL low-voltage safety thresholds for maximum hazardous touch voltage to eliminate the need for high-voltage insulation. [2]
- Shall meet the requirements of NEC, NFPA 70 for low-voltage indoor consumer systems, which defines low-voltage circuits as those operating at 50 V or less and requires compliance with wiring methods specified in Article 725 for Class 1, 2, and 3 circuits, including protection against overcurrent, proper conductor sizing, and insulation rated for the circuit’s voltage. [3]
- Shall avoid use of materials or configurations that violate CPSC safety guidance for consumer electronics, including specification of materials with hazardous chemical content (e.g., lead, phthalates) or components lacking documented compliance with CPSC’s best-practice manufacturing guidance and material-change-testing requirements. [4]
- Shall operate within the safe limits defined by UL 2054 for household and commercial batteries, ensuring that under normal use and foreseeable abuse conditions the battery does not exceed 302°F, remains between 32-140°F while charging, remains between -4–140 °F while discharging, does not catch fire or explode, and is protected against overcharge, short-circuit, mechanical abuse (crush, impact, vibration), and thermal extremes. [5]
- Shall limit external surface temperatures to ≤104 °F (40 °C) during continuous operation, in accordance with UL 94 flammability requirements for plastic materials and the CPSC maximum surface temperature guidelines (16 CFR 1505.7) to prevent thermal hazards. [6] [7]
- Shall use cord sets, flexible cables, and connectors compliant with NEC Article 400, ensuring cords are rated for the system’s voltage and current and provide appropriate insulation and temperature rating, are routed to avoid sharp edges, pinch points, or areas of high foot traffic, with bends maintained above the minimum bend radius, connectors provide proper grounding continuity and are rated for the system’s operating voltage and current, and are secured using clips, cable trays, or protective raceways to minimize tripping hazards and mechanical damage. [8]  
- Shall include grounding, bonding, and electrical protection measures in accordance with OSHA 29 CFR 1910 Subpart S to minimize electrical shock hazards, ensuring all exposed conductive parts are properly grounded and circuit protection devices are installed where required. [9]
- Shall include ANSI Z535.4-compliant safety labels for all user-facing hazards, including moving parts, power indicators, and other electrical or mechanical hazards, ensuring labels are legible, durable, and placed conspicuously to effectively warn users of potential risks. [10] 

## Atomic Subsystem Specifications

#### Processing Unit
The Processing Unit will consist of a Raspberry Pi responsible for coordinating all high-level system operations. Its primary functions are fourfold. First, it will interpret incoming audio signals from the microphone using the Vosk speech recognition engine to convert spoken commands into recognizable text, while also supplying power to the microphone. Second, it will maintain the internal state of the chessboard and verify the legality of player moves using the Stockfish chess engine. Third, it will transmit validated and legal move commands to the Control Unit (Arduino) for conversion into motion control instructions. Lastly, the Raspberry Pi will send display data to the screen, providing the user with real-time visual feedback on system activity and game status.

Functions:

  - Process voice commands and execute chess logic.
  - Coordinate overall system operations.
  - Communicate with user interface (microphone/display) and control logic.
    
Inputs:

  - Voice commands from microphone over USB for easy, reliable compatibility.
  - System status from Control Unit via UART for a simple and reliable method for two way communication. [25]
  - Power from Power Unit.

Outputs:

  - Chess move instructions to Control Unit, also using UART.
  - Feedback to user (via Screen Display) using I2C for a clean and reliable way of communicating. [26]
    
Interfaces:

- Data exchange with Peripherals (Mic, Display).
- Data connection to Control Unit (Arduino).
- Power from Power Unit.
  
High-Level Requirements:

  - Shall process speech using Vosk speech recognition engine.
  - Shall interpret and validate moves using Stockfish chess engine.
  - Shall serve as the central decision-making and coordination hub.

#### Control Unit
The Control Unit will manage all motion control functions and serve as the intermediary between the Processing Unit and the mechanical subsystems. It will receive move instructions from the Raspberry Pi, interpret them into executable signals for the CoreXY motors, and transmit confirmation messages back to the Processing Unit. This will be achieved through the Arduino’s coordination of communication with stepper motor drivers housed within the Control Unit. The servo motor responsible for magnetic actuation will receive direct control signals from the Arduino to ensure precise vertical (Z-axis) movement.

Functions:

  - Translate move instructions into motor control signals.
  - Manage stepper motor drivers for coordinated movement.
  - Relay system status back to the Processing Unit.
    
Inputs:

  - Move commands from Processing Unit, using UART as previously stated.
  - Power from Power Unit.

Outputs:

  - Control signals to motors from motor drivers.
  - Feedback to Processing Unit over UART.
    
Interfaces:

  - Arduino microcontroller.
  - Motor Drivers.
  - Data connection with Processing Unit.
    
High-Level Requirements:

  - Shall convert logical chess moves into physical movement instructions.
  - Shall ensure movement reliability and position accuracy.

#### Core XY Unit
The CoreXY Unit will execute all physical motion required to reposition chess pieces on the board. Upon receiving step and direction commands from the Control Unit, it will drive two stepper motors to manipulate belts and pulleys that move a magnetic carriage across the X and Y axes. A servo-driven magnet will function as the Z-axis actuator, enabling the magnet to raise and lower as needed. This mechanism minimizes magnetic interference with nearby pieces and prevents unintentional displacement during movement.

Functions:

  - Physically move chess pieces on the board using a Core XY mechanism.
    
Inputs:

  - Control signals from motor drivers in Control Unit.
  - Power from Power Unit.

Outputs:

  - Physical movement of chess pieces.
    
Interfaces:

  - Stepper Motors (controlled by drivers).
  - Pulley system (for piece movement).
    
High-Level Requirements:

  - Shall move the chess pieces accurately to specified coordinates.
  - Shall allow for capturing, placing, and repositioning of chess pieces.
  - Shall execute moves smoothly and quietly.

#### Peripherals Unit
The Peripherals Unit consists of the system’s input and output devices — the microphone and display screen. The microphone captures user voice commands, potentially supported by software-based noise filtering to improve accuracy and clarity. The display provides feedback to the player by showing system messages such as “Not a Legal Move” or “Pawn to A5”, as well as overall game status updates. Together, these peripherals form the user interface that enables intuitive interaction with the system.

Functions:

  - Provide user interaction via input and output interfaces.
  - Capture voice commands and display system responses.
    
Inputs:

  - User voice input.
  - Data from Processing Unit, transmitted using I2C for simple and reliable communication. 
  - Power from Power Unit.

Outputs:

  - Display messages, move feedback, and prompts to the user.
  - Microphone output to Processing Unit via USB.
    
Interfaces:

  - Microphone (voice capture).
  - Screen Display (visual output).
  - Data connection with Processing Unit.
    
High-Level Requirements:

  - Shall receive voice input for game commands.
  - Shall display helpful information for the user while playing.

#### Power Unit
The Power Unit supplies regulated electrical power to all other subsystems. It will consist of a battery-based power source designed to provide multiple voltage levels to meet the varying current and voltage requirements of each component. The 12V rail will supply power to the stepper motors and drivers, while the 5V rail will support the Raspberry Pi, Arduino, and other control and peripheral electronics. Proper power regulation and distribution are essential to ensure safe, stable, and efficient system operation.

Functions:

  - Supply consistent power to all subsystems.
  - Enable portable and uninterrupted operation.
    
Inputs:

  - Wall outlet when charging

Outputs:

  - Regulated power to Processing, Control, Core XY, and Peripherals units.
    
Interfaces:

  - Power lines to each subsystem.
    
High-Level Requirements:

  - Shall provide stable power for all electronic components.
  - Shall have a large enough battery for extended gameplay.

# Ethical, Professional, and Standards Considerations

The development of the Chess 2 Impress Audio Actuated Chessboard—a robotic system that enables voice-commanded chess moves, automated piece movement via electromagnets and stepper motors, and integration with chess engines—presents a unique opportunity to blend recreational gaming with accessible technology. This section evaluates the project's ethical implications, professional responsibilities, and adherence to relevant standards, while assessing its broader impacts on culture, society, the environment, public health, public safety, and the economy. These considerations have directly shaped the conceptual design, imposing specific constraints, specifications, and practices to ensure responsible innovation.

## Ethical Situations Expected to Encounter

Several ethical challenges may arise during the project lifecycle. First, privacy concerns stem from the voice recognition component, which processes user audio inputs to interpret chess moves (e.g., "knight to e4"). Without proper safeguards, this could inadvertently capture unrelated conversations or sensitive data, raising issues of data consent and storage. To address this, the design incorporates on-device processing where feasible, and ensures audio is not persistently stored.[27]

Second, accessibility equity is a key ethical tension: while the system aims to include visually impaired players, it could inadvertently exclude those with speech impairments or non-standard accents if the speech-to-text model lacks diversity in training data. Ethical sourcing of datasets (e.g., diverse voice samples) will be prioritized to avoid bias.[28]

Third, intellectual property (IP) risks involve open-source chess engines (e.g., Stockfish) and hardware designs (e.g., Arduino libraries for stepper motors). Unattributed use could lead to plagiarism claims, so all code and schematics will be documented with licenses and contributions credited.[29]

Finally, as a capstone project, team dynamics may introduce ethical dilemmas, such as unequal workload distribution or pressure to prioritize functionality over safety testing. Professional ethics, guided by the ACM Code of Ethics, will mandate transparent collaboration and peer reviews.[30]

## Broader Impacts on the Community

The Chess 2 Impress Audio Actuated Chessboard has predominantly positive, albeit modest, impacts across multiple domains, fostering inclusivity while mitigating potential negatives.

Cultural Impacts: Chess is a global cultural artifact symbolizing strategy and intellectual heritage. This project enhances its cultural relevance by modernizing traditional over-the-board (OTB) play, appealing to younger, tech-savvy demographics and bridging analog and digital divides. It could revive interest in chess clubs or tournaments by making play more engaging and shareable (e.g., via integrated online play), potentially increasing cultural participation in underserved communities.

Societal Impacts: On society, the board promotes cognitive health through accessible chess, which research links to improved problem-solving and memory.[31] For the community—particularly students, hobbyists, and rehabilitation centers—it democratizes gaming, enabling remote or solo play against AI. Broader societal benefits include educational outreach; the open-source design could inspire STEM curricula, encouraging underrepresented groups to engage in robotics and AI. However, if commercialized, it risks widening the digital divide if priced accessibly only to affluent users.[32]

Environmental Impacts: As a low-volume prototype, direct environmental effects are minimal, but the design emphasizes sustainability to model responsible engineering. Components like neodymium magnets and lithium polymer batteries pose e-waste risks if not recycled; [33] thus, modular hardware allows for easy upgrades and disassembly. Compared to mass-produced commercial boards (e.g., Square Off or GoChess), our DIY approach reduces manufacturing emissions by using off-the-shelf parts, potentially lowering the carbon footprint for hobbyist replication.

Public Health Impacts: Positively, the system supports mental health by providing therapeutic, low-physical-effort recreation, ideal for elderly users or those with mobility limitations. Voice actuation reduces screen time versus app-based chess, promoting social interaction in group settings. No significant negative health risks are anticipated, assuming proper electromagnetic shielding to prevent interference with pacemakers.[34]

Public Safety Impacts: Safety is paramount in a device with moving parts (e.g., under-board actuators) and electrical components. Potential hazards include pinching from stepper mechanisms or electrical shorts, but these are mitigated through fail-safes. Overall, the project enhances safety by enabling contactless play, reducing germ transmission in shared environments like schools.

Economic Impacts: For the local community (e.g., university ecosystem), the project boosts skill-building in high-demand fields like AI and mechatronics, potentially leading to startup opportunities or job placements. Economically, an open-source release could spur a niche market for custom boards, benefiting small-scale makers. However, it competes with commercial products, so IP strategies will balance innovation with fair competition.

## Application of Identified Standards

The project has identified key standards organizations that inform the design, ensuring compliance, interoperability, and safety. These include:

IEEE Standards Association (IEEE 802.15.4 for low-power wireless communication): Applied to Bluetooth or Zigbee modules for voice data transmission between the microphone and microcontroller. This standard ensures low-latency, energy-efficient connectivity, critical for real-time move actuation without lag that could frustrate users.[35]

ASTM International (ASTM F963 for toy safety, adapted for recreational devices): Guides material selection and edge rounding on the wooden board to prevent injuries, treating the chessboard as a "toy-like" interactive device.[36]

UL (Underwriters Laboratories) Standards (UL 60950-1 for IT equipment safety): Influences electrical design, specifying insulation and grounding for the 5-24V power supply to avoid shocks or fires.[37]

W3C Web Accessibility Initiative (WCAG 2.1 for voice interfaces): Ensures the speech recognition adheres to accessibility guidelines, such as providing text fallbacks for voice commands and supporting multiple languages/accents.[38]

ISO/IEC 27001 for information security: Applied to any data handling in voice processing, enforcing encryption for transmitted audio snippets.[39]

These standards are not merely checkboxes; they are integrated into the requirements phase via traceability matrices, linking each to testable design elements (e.g., IEEE compliance verified through signal integrity tests).

## Comprehensive Discussion: Influence on the Design

These ethical, professional, and standards considerations have profoundly influenced the conceptual design, transforming abstract concerns into actionable constraints, specifications, and practices. This iterative process—conducted through design reviews and ethical audits—ensures the final product is robust, equitable, and aligned with societal good.

## Key influences include:

Constraints Imposed: Privacy ethics constrained cloud reliance, mandating edge computing on a Raspberry Pi or Arduino, which limits processing power to lightweight models but ensures data sovereignty. Environmental concerns capped component count at <50 units per prototype, favoring reusable parts like salvaged steppers to minimize resource use. Safety standards (UL/ASTM) restricted voltage to 12V max and required physical barriers (e.g., acrylic underlay) around actuators, preventing hazards.

Specifications Derived: Broader societal impacts drove accessibility specs, such as 95% voice command accuracy across accents (tested via diverse datasets) and adjustable audio feedback volumes (WCAG-compliant). Economic and cultural goals specified an open-source license (MIT) for schematics, with modular firmware for easy engine swaps (e.g., Stockfish integration). Professional ethics added logging features for auditing team decisions, ensuring transparency.

Practices Implemented: Standards application manifests in validation protocols: IEEE tests for wireless reliability (e.g., <50ms latency) and ISO security scans for vulnerabilities. These practices address impacts holistically; for instance, public health specs include haptic feedback alternatives to voice, reducing exclusion risks, while economic practices like cost modeling (<$200 BOM) promote community replication.

In summary, these considerations elevate the project from a novel gadget to a thoughtful intervention in accessible gaming. By embedding them early, the design complies with expectations and allows for future scalability. Ongoing monitoring via post-prototype surveys will refine these elements, embodying continuous professional improvement.

## Resources

### Budget
The following section outlines the estimated costs associated with each subsystem, including justifications for major components and materials.
#### Processing Unit
| Item | Description / Notes | Quantity | Approx. Cost (USD) |
| --- | --- | --- | --- |
| **Raspberry Pi** | Handles high-level logic, Stockfish chess engine, and Vosk speech recognition; coordinates all subsystems | 1 | $50–$60 |
| **MicroSD Card** | Stores OS, chess engine, and voice recognition software | 1 | $6–$10 |

The Processing Unit is the computational core of the system. A Raspberry Pi should be chosen for its balance of performance and cost, capable of running Stockfish and the Vosk speech engine simultaneously. A MicroSD card provides non-volatile storage for the operating system and application software.
#### Control Unit
| Item | Description / Notes | Quantity | Approx. Cost (USD) |
| --- | --- | --- | --- |
| **Arduino** | Converts Pi commands into motor control signals; interfaces with stepper drivers | 1 | $20–$30 |
| **Stepper Driver Boards** | Amplify control signals and drive the stepper motors | 2 | $5–$10 each |

The Control Unit acts as the intermediary between the Processing Unit and the mechanical motion subsystem. The Arduino chosen should provide precise control timing for motor drivers and support flexible integration with the magnet mechanism. Dual stepper drivers enable independent X and Y axis movement.
#### CoreXY Unit
| Item | Description / Notes | Quantity | Approx. Cost (USD) |
| --- | --- | --- | --- |
| **Stepper Motors** | Drive CoreXY belts to move the magnetic carriage | 2 | $10–$12 each |
| **Belt and Pulley Set** | Transmits motion from motors to carriage | 1 set | $8–$10 |
| **CoreXY / XY Framework** | Includes rails, idlers, carriage, and frame | 1 | $40–$65 |
| **Magnet Assembly** | Moves chess pieces via magnetic coupling | 1–2 | $15–$20 |

The CoreXY Unit performs all physical motion, requiring precise linear motion components. Stepper motors provide high positional accuracy, while the belt-and-pulley system converts rotational motion into planar movement. The magnet mechanism allows non-contact manipulation of chess pieces.
#### Peripherals Unit
| Item | Description / Notes | Quantity | Approx. Cost (USD) |
| --- | --- | --- | --- |
| **Microphone** | Captures user voice commands for recognition | 1 | $8–$10 |
| **Display Screen** | Provides system feedback, messages, and game status | 1 | $12–$18 |

The Peripherals Unit establishes user interaction. A microphone allows for voice-based input processed by the Raspberry Pi, while a display delivers visual feedback and system prompts.
#### Power Unit
| Item | Description / Notes | Quantity | Approx. Cost (USD) |
| --- | --- | --- | --- |
| **Power Supply** | Provides regulated power to motors, Pi, and control electronics | 1 | $30–$40 |

A stable, regulated power supply is essential for reliable operation. The system should support both a 12V line supports the stepper motors and drivers, and a 5V output powers logic components and peripherals. Proper power distribution ensures electrical safety and prevents system instability.
#### Miscellaneous/Structural Components
| Item | Description / Notes | Quantity | Approx. Cost (USD) |
| --- | --- | --- | --- |
| **Chessboard Frame (Wood or 3D Printed)** | Supports CoreXY mechanism and aesthetic housing | 1 | $20–$30 |
| **Chess Piece Set (Metal Base)** | Enables magnetic manipulation | 1 | $15–$25 |
| **Prototyping and Miscellaneous Materials** | Spare wiring, connectors, mounts, testing supplies | — | $150 |

These components complete the mechanical and visual integration of the system. The chessboard frame houses the motion platform, while magnetized pieces enable interaction. The prototyping budget accounts for iteration and testing materials necessary for functional validation.
#### Comprehensive Budget Summary
| Subsystem | Estimated Cost Range (USD) |
| --- | --- |
| Processing Unit | $56–$70 |
| Control Unit | $30–$50 |
| CoreXY Unit | $73–$107 |
| Peripherals Unit | $20–$28 |
| Power Unit | $30–$40 |
| Structural Components | $35–$55 |
| **Estimated System Cost** | **≈ $244 – $350** |
| **Prototyping Cost** | **$150** |
| **Estimated Total Cost** | **≈ $394 – $500** |

### Division of Labor

Each team member was assigned to a subsystem that best matches their technical strengths, ensuring efficient development and balanced workload across hardware and software domains.

#### Nathan MacPherson – Peripherals Unit
Nathan’s skills in Digital Systems, Programming, Networks, and Electrical CAD align with integrating the microphone and display. His experience supports reliable data communication and hardware interfacing with the Processing Unit.

#### Noah Beaty – Control Unit
Noah’s background in Microcontrollers, Programming, and Networking fits the Arduino-driven Control Unit, where precise motor control and communication with the Processing Unit are key.

#### Jack Tolleson – Processing Unit
With strengths in Programming, Digital Systems, and Microcontroller knowledge, Jack is well-suited for the Raspberry Pi–based Processing Unit, handling speech recognition, chess logic, and coordination between subsystems.

#### Allison Givens – CoreXY Unit
Allison’s expertise in CAD, 3D Printing, and Microcontroller programming supports the CoreXY mechanical subsystem, combining hardware design with control integration for accurate motion.

#### Lewis Bates – Power Unit
Lewis’s knowledge of Embedded Systems and Power Electronics makes him ideal for managing the Power Unit, ensuring stable, efficient energy delivery to all components.

### Timeline



## References

[1] U.S. Federal Communications Commission, “47 CFR Part 15, Subpart B: Unintentional Radiators,” Electronic Code of Federal Regulations, Title 47, Chapter I, Subchapter A, Part 15, Subpart B. [Online]. Available: https://www.ecfr.gov/current/title-47/chapter-I/subchapter-A/part-15/subpart-B. Accessed: Oct. 27, 2025.

[2] U.S. company UL Solutions, “Protection from Electrical Hazards,” Nov. 2024. [Online]. Available: https://www.ul.com/resources/protection-electrical-hazards. [Accessed: Oct. 28 2025].

[3] National Fire Protection Association, NFPA 70, National Electrical Code®, 2017 ed. Quincy, MA: NFPA, 2016.

[4] U.S. Consumer Product Safety Commission, “Manufacturing Best Practices,” Business Education, Manufacturing, [Online]. Available: https://www.cpsc.gov/business--manufacturing/business-education/business-guidance/BestPractices. [Accessed: Oct. 28 2025].

[5] Underwriters Laboratories, UL 2054 Standard for Household and Commercial Batteries, 3rd ed., Nov. 17 2021.

[6] Underwriters Laboratories, UL 94: Standard for Safety of Flammability of Plastic Materials for Parts in Devices and Appliances, 5th ed., Northbrook, IL: UL, 2024.

[7] U.S. Consumer Product Safety Commission, “Maximum acceptable surface temperatures,” Code of Federal Regulations, Title 16, Part 1505.7. [Online]. Available: https://www.law.cornell.edu/cfr/text/16/1505.7. [Accessed: Oct. 28, 2025].

[8] National Fire Protection Association, NFPA 70, National Electrical Code®, 2023 ed., Quincy, MA: NFPA, 2022.

[9] U.S. Occupational Safety and Health Administration, OSHA Standards – Subpart S: Electrical, 29 CFR 1910, Washington, D.C.: OSHA, 2025.

[10] American National Standards Institute, ANSI Z535.4: Product Safety Signs and Labels, 2011 ed., Washington, DC: ANSI, 2011.

[11] U.S. Government, Rehabilitation Act of 1973, Section 508, Washington, DC, 1998.

[12] American National Standards Institute / Human Factors and Ergonomics Society, ANSI/HFES 100-2007: Human Factors Engineering of Computer Workstations, 2007.

[13] Center for Universal Design, Principles of Universal Design, North Carolina State University, 1997.

[14] "Wlkata Mirobot Professional Kit - 6 Axis Robotic Arm - Ros & Matlab Simulation Teaching," Wlkata, 2025. https://www.wlkata.com/products/professional-kit-of-wlkata-mirobot-six-axis-robot-arm-robotic-arm-k12-education-equipment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

[15] "Chessnut Move | Review | Are you ready for robot chess?," Adventures of a Chess Noob, Jul. 08, 2025. https://adventuresofachessnoob.com/2025/07/08/%F0%9F%94%A5-chessnut-move-review-are-you-ready-for-robot-chess-%F0%9F%A4%96%E2%99%9F%EF%B8%8F%F0%9F%A4%94/

[16] Chessnutech. (n.d.). Chessnut move - advanced robotic chessboard with Plastic Pieces. Chessnut. https://www.chessnutech.com/products/chessnut-move-advanced-robotic-chessboard-with-plastic-pieces

[17] Admin, "Why the Core3D printer uses CoreXY," Core3D Custom Printers, Jun. 10, 2017. https://core3d.tech/2017/06/10/why-core3d-printer-uses-corexy/

[18] H. M. | R. Pi | 0, "How to Use DC Motors on the Raspberry Pi," Circuit Basics, Jun. 10, 2021. https://www.circuitbasics.com/introduction-to-dc-motors/

[19] ella, "Transform Your Raspberry Pi Into a Powerful Cloud Storage Server - Pidora," Pidora, Feb. 08, 2025. https://pidora.ca/transform-your-raspberry-pi-into-a-powerful-cloud-storage-server/

[20] "Raspberry Pi Arduino Serial Communication - Everything You Need To Know," The Robotics Back-End, Nov. 11, 2019. https://roboticsbackend.com/raspberry-pi-arduino-serial-communication/

[21] "AC-DC Universal Power Adapter Multi Voltage Output: 1.5VDC-12VDC @ 1000 mA; 7-plugs," AC-DC PowerShack, 2020. https://www.acdcpowershack.com/products/ac-dc-universal-power-adapter-multi-voltage-output-1-5vdc-12vdc-1000-ma-7-plugs-part-hc-1000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

[22] J. Hanna, “Wireless AC/DC Module," PASCO scientific, 2019. https://www.pasco.com/products/lab-apparatus/electricity-and-magnetism/circuits-and-components/wireless-ac-dc-module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

[23] "EXTRALINK Power Supply with Battery Charger 12V/13.8V 55W (EL-PSUPPLY-AD-55A) - The source for WiFi products at best prices in Europe - wifi-stock.com," Wifi-stock.com, 2025. https://www.wifi-stock.com/details/extralink-power-supply-with-battery-charger-12v13-8v-55w-el-psupply-ad-55a.html

[24] Instructables, "Audio Visualizer With an LCD Display," Instructables, Jun. 07, 2022. https://www.instructables.com/Audio-Visualizer-With-an-LCD-Display/

[25] “Understanding UART,” Rohde & Schwarz, 2025. https://www.rohde-schwarz.com/us/products/test-and-measurement/essentials-test-equipment/digital-oscilloscopes/understanding-uart_254524.html

[26] Joseph Wu, “A Basic Guide to I2C,” Texas Instruments Application Note SBAA565, November 2022. https://www.ti.com/lit/an/sbaa565/sbaa565.pdf

[27] National Institute of Standards and Technology. (2021). NIST Privacy Framework: A Tool for Improving Privacy through Enterprise Risk Management, Version 1.0. https://doi.org/10.6028/NIST.CSWP.01162021

[28] Buolamwini, J., & Gebru, T. (2018). Gender Shades: Intersectional Accuracy Disparities in Commercial Gender Classification. Proceedings of Machine Learning Research, 81, 77–91. http://proceedings.mlr.press/v81/buolamwini18a.html

[29] Stockfish. (2024). Stockfish Open Source Chess Engine – License. GitHub Repository. https://github.com/official-stockfish/Stockfish/blob/master/COPYING

[30] Association for Computing Machinery. (2018). ACM Code of Ethics and Professional Conduct. https://www.acm.org/code-of-ethics

[31] Sala, G., & Gobet, F. (2017). Does chess instruction improve mathematical problem-solving ability? Two experimental designs and a meta-analysis. Frontiers in Psychology, 8, 1981. https://doi.org/10.3389/fpsyg.2017.01981

[32] Warschauer, M., & Matuchniak, T. (2010). New technology and digital worlds: Analyzing evidence of equity in access, use, and outcomes. Review of Research in Education, 34(1), 179–225. https://doi.org/10.3102/0091732X09349791

[33] United Nations Environment Programme. (2020). Global E-waste Monitor 2020. https://ewastemonitor.info/

[34] U.S. Food and Drug Administration. (2021). Electromagnetic Compatibility (EMC) of Medical Devices – Guidance for Industry and Food and Drug Administration Staff. https://www.fda.gov/regulatory-information/search-fda-guidance-documents/electromagnetic-compatibility-emc-medical-devices

[35] IEEE Standards Association. (2020). IEEE Std 802.15.4-2020: Low-Rate Wireless Personal Area Networks (LR-WPANs). https://standards.ieee.org/standard/802_15_4-2020.html

[36] ASTM International. (2023). ASTM F963-23: Standard Consumer Safety Specification for Toy Safety. https://www.astm.org/f0963-23.html

[37] Underwriters Laboratories. (2019). UL 60950-1: Information Technology Equipment – Safety – Part 1: General Requirements (now superseded by UL 62368-1, but referenced for legacy applicability). https://www.shopulstandards.com

[38] World Wide Web Consortium. (2018). Web Content Accessibility Guidelines (WCAG) 2.1. https://www.w3.org/TR/WCAG21/

[39] International Organization for Standardization. (2022). ISO/IEC 27001:2022 – Inform

[40] circuitgeeks, "Arduino Buttons and LEDs | Push Button Tutorial," Circuit Geeks, Jan. 16, 2022. https://www.circuitgeeks.com/arduino-push-button-tutorial/

[41] E. Electronics et al., "Simple Microphone to Speaker Amplifier Circuit," Circuit Digest, Nov. 13, 2018. https://circuitdigest.com/electronic-circuits/simple-microphone-to-speaker-circuit

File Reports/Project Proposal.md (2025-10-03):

# Chess 2 Impress

## Introduction

As chess continues to grow in popularity, the demand for new, more interesting chess technology has become increasingly apparent. One of the newest innovations made to meet this demand is the automated chess board. Automated chess boards are capable of moving each piece around the board without human intervention, allowing users to play over the board against computers, people with disabilities, and friends across the world. Although this advancement has provided many new and exciting opportunities in the world of chess, automated boards prove to be too expensive for widespread use by average consumers. This project aims to design an automated chess board at a cheaper price, providing its benefits to more people around the world.

The remainder of this proposal will:

- Identify and further define the problems with current automated chess boards.

- Create specifications and constraints for voice input, piece movement, accessibility, safety, and affordability.

- Examine current automated chess boards in greater detail, identifying where they can be improved.

- Define ways to measure this chess board's effectiveness and successfulness.

- List what resources will be needed and used to create the chess board.

- Discuss the outward implications this chess board may have to wider audiences.

## Formulating the Problem

Current automated chess boards are expensive and lack features such as online functionality, voice recognition, and unobstructed movement. The goal of this implementation is to improve these features, reduce cost, use accessible parts for easy hobbyist replication, and to make the game more accessible for players with disabilities. Beyond individual use, this new technology could attract new customers to businesses related to board games or leisure locations through its novelty and fascination. Challenges of this project include digital signal processing for voice controls, artificial intelligence (AI) implementation for solo-play, and automating piece movement. 

### Background

During the pandemic, chess increased in popularity [13]. Online chess specifically had a major influx of activity, with Chess.com adding 1 million accounts from March to November 2020, and a 2.8 million member increase in November alone [13]. This newfound popularity opens up opportunities for innovation on this classic game. An automated chess board would support primarily online chess players who want to improve their over-the-board (OTB) game.

AI has had a major impact in the world of chess, especially in the context of online play [6]. It provides learning opportunities, as certain AI can beat any human player. Chess games played OTB do not usually have this capability except for automated boards. AI in OTB implementations will allow players to improve by progressively increasing the strength of their opponent. This function would aid online players transitioning to OTB play, as they could play against AI before a human opponent. This feature also supports those who want to play OTB chess but cannot do so alone.

Many efforts have been made to ensure that chess tournaments are accommodating to those with disabilities [17]. These accommodations still could be improved upon for player autonomy and ease in preparing. For those with Alzheimer’s, other dementias, dyslexia, dysgraphia, fine/gross motor needs, who are blind, or those with a temporary disability such as a broken hand, an accommodation that can be made is the assignment of a Game Assistant (GA) [17]. In cases such as these, the GA may be needed for piece movement, clock pressing, and/or scoring [17]. An automated board could help as an alternative to a GA by helping with piece movement, automatically keeping time, and automating scoring. This would allow players more independence, as they would not have to rely on the assistance of a GA, and fewer volunteers would be needed for tournaments.

## Specifications

The chessboard will meet the following requirements to ensure reliability and operability:

1. **Voice Input**

    - Board shall recognize voice input with an accuracy of at least 80%.
    - Board shall listen for input while a button is pressed or after a command word is spoken to avoid accidental moves.
    - Board shall recognize commands in algebraic chess notation and other common variations (Knight to e5, Bishop a4, etc.).
    - Board shall process commands within 5 seconds of button release or end of voice command.
2. **Automated Piece Movement**

    - Board shall move pieces within half an inch of the center of each square.
    - Board shall ensure that all pieces remain upright and stable while moving.
    - Board shall finish any single-piece move within 5 seconds of beginning the movement.
    - Board shall notice and remove 95% of captured pieces without piece collision.
3. **Portability and Accessibility**

    - Board shall weigh less than 30 pounds such that one person can move it.
    - Board shall have labels on each file and rank to assist users in locating each square.
    - Board may have a carrying case or handle.
4. **Power and Safety**

    - Board shall have a sleep mode to reduce power consumption when not in immediate use.
    - Board shall be powered by a 12V DC adapter or rechargeable battery supporting at least 2 hours of active gameplay.
5. **Affordability and Modifications**

    - Board shall cost no more than $350 USD in materials
    - Board shall have a modular design allowing for upgrades to individual systems.
## Constraints
The chessboard will be designed to operate efficiently while adhering to the following safety and regulatory requirements:

1. **Regulatory and Compliance Constraints**

    - Board shall comply with FCC Part 15, Subpart B (Class B) regulations, ensuring that electromagnetic interference is within acceptable limits for residential and public environments.
    - Board shall operate below 50V DC in accordance with UL low-voltage safety thresholds, removing the need for additional electrical insulation and protection.
    - Board shall meet applicable requirements of the National Electrical Code (NEC NFPA 70) for low-voltage consumer electronic systems intended for indoor use.
    - Board shall avoid materials or component configurations that would violate CPSC (Consumer Product Safety Commission) regulations regarding consumer electronics used in public settings.

2. **Electrical and Safety Constraints**

    - Board shall prevent hazardous surface temperatures, maintaining an external temperature of no more than 104°F (40°C) under continuous operation, per UL 94 and general consumer safety guidelines.
    - Board shall utilize standard cord sets and connectors compliant with NEC Article 400 to ensure safe installation and minimal tripping or disconnection hazards in public spaces.
    - Board shall ensure proper grounding and protection of all power connections to conform to OSHA 1910 Subpart S electrical safety practices for general-use electronic systems.
    - Board shall display clear warning labels for user-facing hazards (e.g., moving parts, power status) in accordance with ANSI Z535.4 standards for safety signage and communication.

3. **Accessibility and Ergonomic Constraints**

    - Board shall conform to Section 508 of the Rehabilitation Act for electronic systems, ensuring digital interfaces (e.g., voice command, status indicators) are accessible to users with disabilities.
    - Board shall follow ergonomic interface design principles from ANSI/HFES 100-2007, including appropriate control placement, spacing, and feedback mechanisms.
    - Board shall avoid design elements that may cause confusion or usability issues for individuals with cognitive or motor impairments, adhering to universal design principles where possible.
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

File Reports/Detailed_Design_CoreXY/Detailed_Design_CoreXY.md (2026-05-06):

# CoreXY Detailed Design

This document presents a comprehensive overview of the CoreXY subsystem, one of the five primary components of the automated chessboard system; other subsystems consist of the Processing Unit (PU), Control Unit (CU), Power Unit, and Peripherals Unit. While the primary focus is on the CoreXY, this document also provides a high-level integration perspective with the remaining subsystems, in order to illustrate the CoreXY’s role in  physically implementing piece movement within the entire system. Additionally, the document outlines the key technical constraints, relevant electrical and safety standards, and operational requirements that guide the subsystem’s design and implementation. Finally, it describes the proposed mechanical architecture, magnetic actuation method, flux calculations, and motion transmission calculations necessary to construct and validate the CoreXY as a critical part of the complete automated chessboard solution.

## Function of the Subsystem

The CoreXY subsystem serves as the mechanical motion platform responsible for executing physical piece movement across the chessboard. Operating under command signals received from the Control Unit, the CoreXY translates high-level motion instructions into precise two-dimensional movement along the X and Y axes. The system utilizes a belt-driven CoreXY configuration, where two stepper motors generate coordinated linear motion of a magnetic actuator mounted beneath the playing surface [1].
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

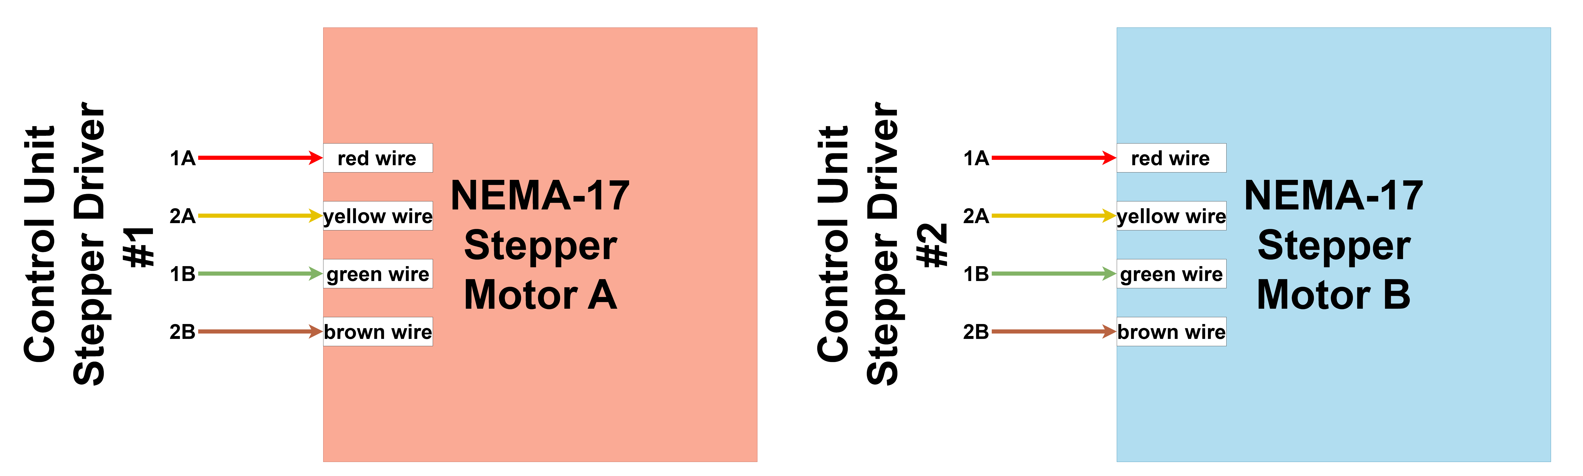
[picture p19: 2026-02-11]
images/Schematics/Stepper_Motors_Schematic.png

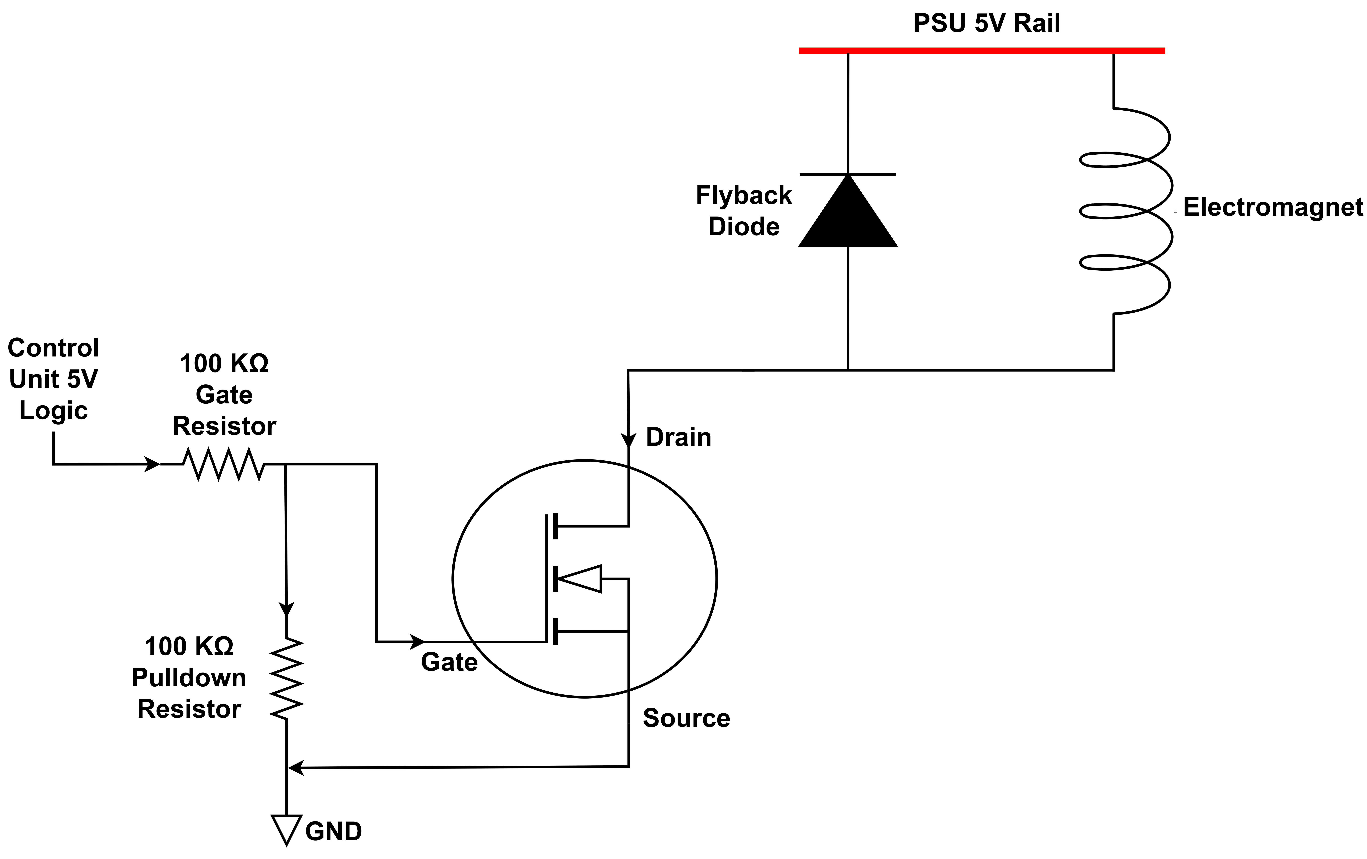
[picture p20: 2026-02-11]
Reports/Detailed_Design_CoreXY/images/Schematics/EM_Schematic.png

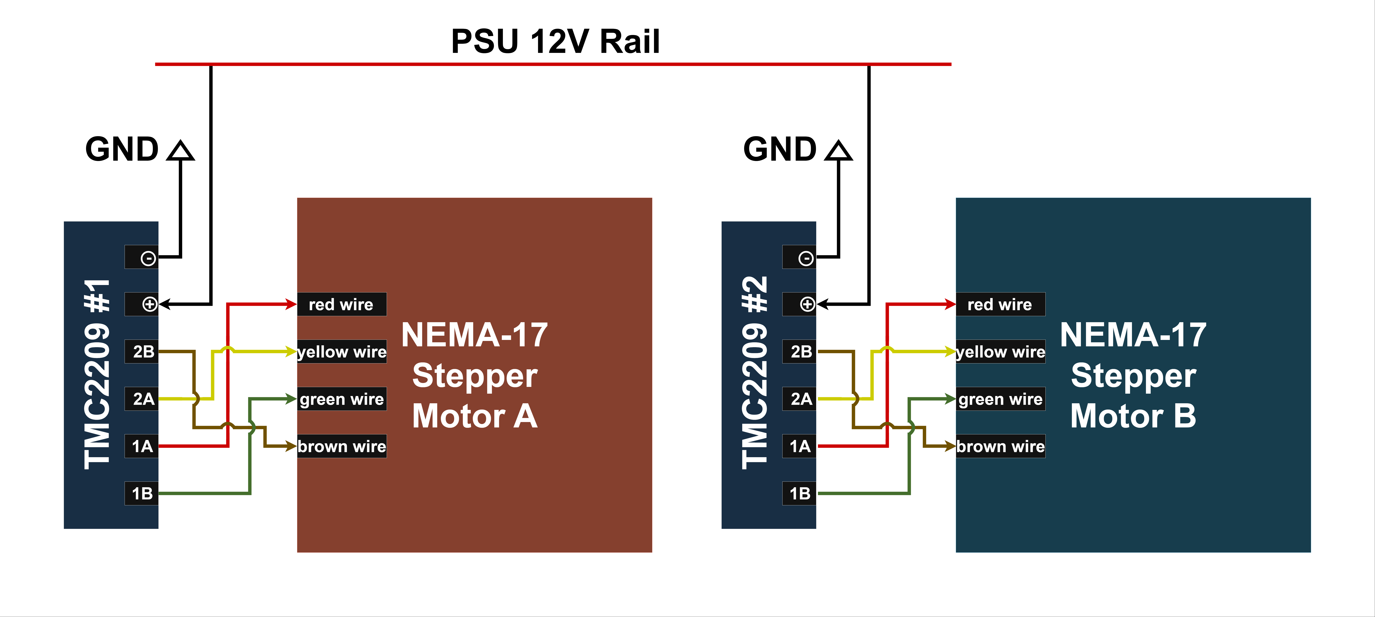
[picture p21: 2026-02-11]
Reports/Detailed_Design_CoreXY/images/Schematics/Stepper_Motors_Schematic.png

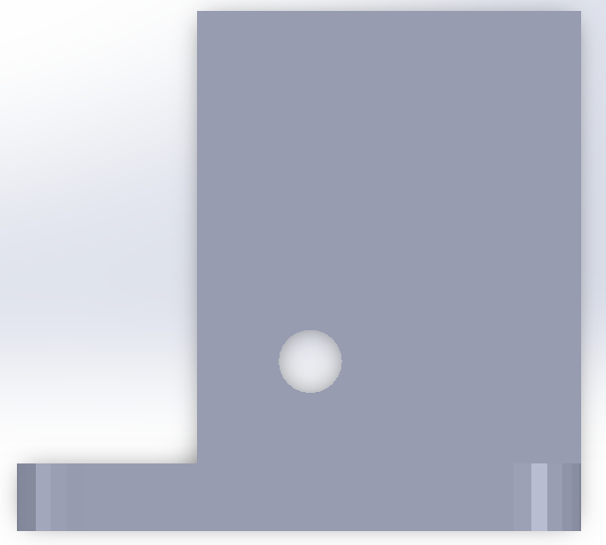
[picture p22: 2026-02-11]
Reports/Detailed_Design_CoreXY/images/Models/Front_Motor_Support_A.png

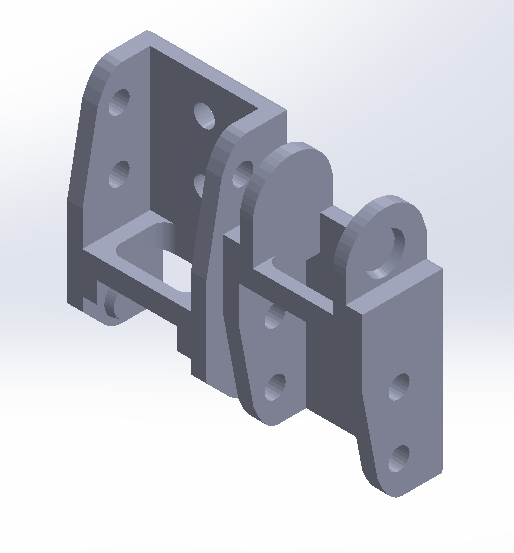
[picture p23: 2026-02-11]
Reports/Detailed_Design_CoreXY/images/Models/Isometric_Cable_Ends.png

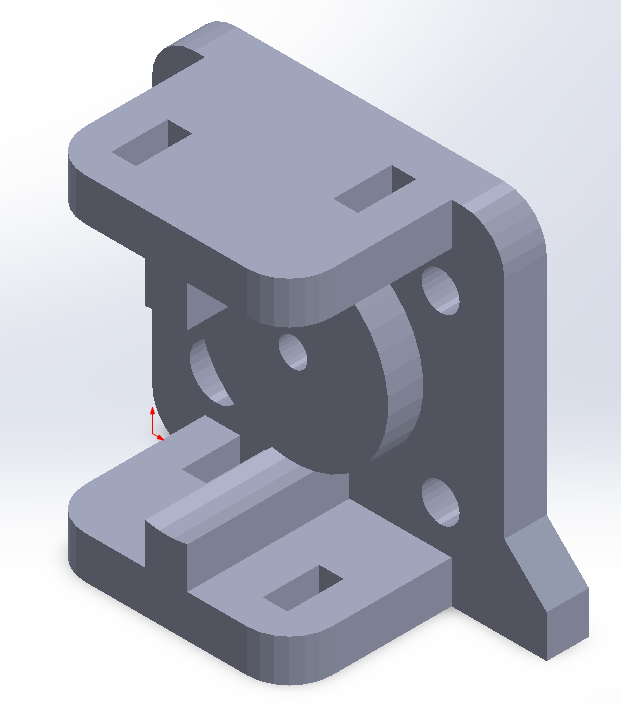
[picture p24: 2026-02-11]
Reports/Detailed_Design_CoreXY/images/Models/Isometric_Electro_Support.png

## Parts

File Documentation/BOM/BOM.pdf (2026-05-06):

Item | Description | Quantity | Distributor | Distributor ID | Storage Location | Date Acquired | Condition | Notes
1 | Arduino Nano 1 | | Arduino A000005 | | In use | Tuesday, March 3, 2026 New | | Used for project
2 | Stepper Driver Board (Heatsink Included) 2 | | Adafruit 6121 | | Two used, rest in Station 9, Box 1 | Tuesday, March 3, 2026 New | | Used for project
3 | Stepper Driver Heatsink 2 | | Adafruit 1493 | | Station 9, Box 1 | Tuesday, March 3, 2026 New | | Not Used, not returned
4 | MOSFET 1 | | Digikey IRLZ44NPBF-ND | | In use | Tuesday, March 3, 2026 New | | Used for project
5 | Flyback Diode 1 | | Digikey 1655-1019-ND | | In use | Tuesday, March 3, 2026 New | | Used for project
6 | Pulldown Resistor 1 | | Digikey 13-CFR-25JB-52-100K-ND | | In use | Tuesday, March 3, 2026 New | | Used for project
7 | Gate Resistor 1 | | Digikey 13-MFR-25FRF52-100RCT-ND | | In use | Tuesday, March 3, 2026 New | | Used for project
8 | Perfboard 1 | | Digikey 1528-4785-ND | | In use | Tuesday, March 3, 2026 New | | Used for project
9 | UPS HAT for Raspberry Pi 1 | | DFRobot FIT0992 | | In use | Friday, February 27, 2026 New | | Used for project
10 | Raspberry Pi Power Supply (5V/5A USB-C) 1 | | Raspberry Pi SC0510 | | In use | Friday, February 27, 2026 New | | Used for project
11 | MT3608 Step-Up Converter Module 1 | | Amazon B07RNBJK5F | | In use, extras and damaged in Station 9, Box 5 | Friday, February 27, 2026 New | | Used for project
12 | Adafruit AdjusStation Buck Converter (to 3.3V) 1 | | Adafruit 2745 | | Station 9, Box 5 | Friday, February 27, 2026 New | | Not Used, not returned
13 | SparkFun Logic Level Converter (Bi-Directional) 1 | | SparkFun BOB-12009 | | In use | Tuesday, March 3, 2026 New | | Used for project
14 | 18650 Rechargeable Li-ion Batteries (3500mAh each) 4 | | IMR Batteries INR18650-35E | | In use | Friday, February 27, 2026 New | | Used for project
15 | Inline Fuse Holders with Fuses (various ratings) 1 | | Amazon B07D3QKF5S | | Station 9, Box 5 | Tuesday, March 3, 2026 New | | Not Used, not returned
16 | Pi Switch (for safe shutdown) 1 | | PiShop.us Pi-Supply-Switch | | Station 9, Box 5 | Friday, February 27, 2026 New | | Not Used, not returned
17 | Jumper Wires (Female-to-Male, 8-inch) 1 | | Amazon B01LZF1ZSZ | | In use, extras in Station 9, Box 5 | Friday, February 27, 2026 New
18 | 26-pin GPIO male to female extension for Raspberry Pi 1 | | Adafruit 2101 | | Station 9, Box 2 | Friday, February 27, 2026 New | | Not Used, not returned
19 | 26-pin GPIO Ribbon Cable for Raspberry Pi 1 | | Adafruit 862 | | Station 9, Box 2 | Friday, February 27, 2026 New | | Not Used, not returned
20 | USB A to Mini-B cable (power/programming for Arduino Nano) 1 | | Amazon B09DCLRYH6 | | One used, other in Station 9, Box 1 | Tuesday, March 3, 2026 New | | One Used, One not used, not returned
21 | Grove Electromagnet 1 | | Mouser 713-101020073 | | Station 9, Box 4 | Friday, February 27, 2026 New | | Not Used, not returned
22 | Nema 17 Stepper Motor 2 | | Adafruit 324 | | In use | Tuesday, March 3, 2026 New | | Used for project
23 | GT2 Timing Belt, 10 m (6 mm width, 2 mm pitch) 1 | | Amazon 3DP AMZN-10160 | | In use, leftover belt in Station 9, Box 4 | Friday, February 27, 2026 New | | Used for project
24 | GT2 Belt Pulley (16-tooth) 2 | | McMaster-Carr 3684N12 | | In use | Friday, February 27, 2026 New | | Used for project
25 | Idler Pulley, Aluminum 1 | | Amazon B07RV2T54M | | In use, extras in Station 9, Box 4 | Friday, February 27, 2026 New | | Used for project
26 | 3D Printer Rollers 1 | | Amazon B08B4JDB67 | | In use, extras in Station 9, Box 4 | Friday, February 27, 2026 New | | Used for project
27 | Aluminum Extrusion Kit (2020 T-slot, 4x1220 mm) 1 | | Amazon B0CLGX27MY | | In use, extras in Station 9, Box 4 | Friday, February 27, 2026 New | | Used for project
28 | 2020 Aluminum Extrusion Corner Bracket Kit 1 | | Amazon B0FLD88X6Y | | In use, extras in Station 9, Box 4 | Friday, February 27, 2026 New | | Used for project
29 | 3.5 inch LCD Screen 1 | | Amazon B0BJDTL9J3 | | Capstone Lab West Side Closet | Tuesday, March 3, 2026 New | | Not Used, damaged
30 | Mounted USB Coupler 1 | | Amazon B0DT4D13CK | | Station 9, Box | Tuesday, March 3, 2026 New | | Used for project
31 | USB Microphone 1 | | Amazon B08ZQSCJS3 | | In use, case in Station 9, Box 3 | Friday, February 27, 2026 New | | Used for project
32 | 3/4 inch x 2 ft x 4 ft Plywood (Sides) 1 | | Lowe's 6654 | | In use | Friday, March 6, 2026 New | | Used for project
33 | 1/2 inch x 4 foot x 8 foot Plywood (Bottom) 1 | | Lowe's 786167 | | In use, scrap wood propped against Station 9/10 | Friday, March 6, 2026 New | | Used for project, leftover in Capstone Lab
34 | 30 1" Steel Fender Washers 2 | | Lowe's 2215 | | Station 9, Box 3 | Friday, March 6, 2026 New | | Not Used, not returned
35 | 1 1/2 in. Drywall Screws, 50ct 1 | | Lowe's 68135 | | Station 9, Box 3 | Friday, March 6, 2026 New | | Used for project
36 | 5mm - 0.8 x 20-mm Phillips -Drive Machine screws 2 | | Lowe's 999994844 | | In use, extras in Station 9, Box 4 | Friday, March 6, 2026 New | | Used for project
37 | 5mm x 0.8 Zinc-plated Steel Hex Nut 1 | | Lowe's able | | In use, extras in Station 9, Box 4 | Friday, March 6, 2026 New | | Used for project
38 | 3mm - 0.5 x 10-mm Phillips -Drive Machine screws 1 | | Lowe's 999994826 | | In use, extras in Station 9, Box 4 | Friday, March 6, 2026 New | | Used for project
39 | Screws 1.6mm 1 | | Amazon B0192PBLX8 | | In use, extras in Station 9, Box 1 | Wednesday, March 25, 2026 New | | Used for project
40 | Quick Blow Glass Tube Fuse 1 | | Amazon B07YC5ZTMV | | In use, extras in Station 9, Box 5 | Wednesday, March 25, 2026 New | | Used for project
41 | Inline Screw Type Fuse Holder 2 | | Amazon B07SPS14WX | | Station 9, Box 5 | Wednesday, March 25, 2026 New | | Not Used, not returned
42 | Inline Screw Type Fuse Holder 2 | | Amazon B07SN9RG2Q | | In use, extras in Station 9, Box 5 | Wednesday, March 25, 2026 New | | Used for project
43 | Inline Fuse Holder 12V 2 | | Amazon B0D7D25G62 | | Station 9, Box 5 | Wednesday, March 25, 2026 New | | Not Used, not returned
44 | LCD Screen 1 | | Amazon B0B1MK3SQ2 | | In use, leftover cables in Station 9, Box 2 | Wednesday, March 25, 2026 New | | Used for project
45 | Uart cable for rpi 1 | | Digikey 1568-CAB-28698-ND | | In use | Wednesday, March 25, 2026 New | | Used for project
46 | Felt Pads 1 | | Amazon B0FN41J1D5 | | In use, extras in Station 9, Box 3 | Wednesday, March 25, 2026 New | | Used for project
47 | Wood Glue 1 | | Amazon B0006U20NY | | Station 9, Box 3 | Wednesday, March 25, 2026 New | | Not used, substituted for glue in Jeff's shop
48 | Standalone Electromagnet | | Digikey 1528-2689-ND In use | | | Monday, March 30, 2026 New | | Used for project
49 | 40mm Fans 1 | | Amazon B08ZY7X4CR | | In use | Thursday, April 9, 2026 New | | Used for project
50 | Raspberry Pi 5 1 | | PiShop.us SC1111 | | In use | Wednesday, April 22, 2026 New | | Used for project
51 | Neodymium Magnets (to put in base of each piece) 1 | | Amazon D03125H0125 | | In use, extras in Station 9, Box 4 | Wednesday, April 22, 2026 New | | Used for project
52 | Acrylic Sheet 2 | | Dr. Van Neste's Lab N/A | | In use, extras returned to Dr. Van Neste's Lab | Wednesday, April 8, 2026 Used | | Used for project
53 | Mini HDMI to HDMI Cable 1 | | Capstone Lab N/A | | In use | Wednesday, April 8, 2026 Used | | Used for project
54 | Raspberry Pi Active Cooler 1 | | PiShop.us SC1148 | | In use | Wednesday, April 22, 2026 New | | Used for project
55 | Pin Headers 1 | | Dr. Van Neste's Lab N/A | | Half used, rest in Station 9, Box 2 | Wednesday, April 8, 2026 Used | | Used for project

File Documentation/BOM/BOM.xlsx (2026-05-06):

Item | Description | Quantity | Distributor | Distributor ID | Storage Location | Date Acquired | Condition | Notes
1 | Arduino Nano | 1 | Arduino | A000005 | In use | 2026-03-03 | New | Used for project
2 | Stepper Driver Board (Heatsink Included) | 2 | Adafruit | 6121 | Two used, rest in Station 9, Box 1 | 2026-03-03 | New | Used for project
3 | Stepper Driver Heatsink | 2 | Adafruit | 1493 | Station 9, Box 1 | 2026-03-03 | New | Not Used, not returned
4 | MOSFET | 1 | Digikey | IRLZ44NPBF-ND | In use | 2026-03-03 | New | Used for project
5 | Flyback Diode | 1 | Digikey | 1655-1019-ND | In use | 2026-03-03 | New | Used for project
6 | Pulldown Resistor | 1 | Digikey | 13-CFR-25JB-52-100K-ND | In use | 2026-03-03 | New | Used for project
7 | Gate Resistor | 1 | Digikey | 13-MFR-25FRF52-100RCT-ND | In use | 2026-03-03 | New | Used for project
8 | Perfboard | 1 | Digikey | 1528-4785-ND | In use | 2026-03-03 | New | Used for project
9 | UPS HAT for Raspberry Pi | 1 | DFRobot | FIT0992 | In use | 2026-02-27 | New | Used for project
10 | Raspberry Pi Power Supply (5V/5A USB-C) | 1 | Raspberry Pi | SC0510 | In use | 2026-02-27 | New | Used for project
11 | MT3608 Step-Up Converter Module | 1 | Amazon | B07RNBJK5F | In use, extras and damaged in Station 9, Box 5 | 2026-02-27 | New | Used for project
12 | Adafruit AdjusStation Buck Converter (to 3.3V) | 1 | Adafruit | 2745 | Station 9, Box 5 | 2026-02-27 | New | Not Used, not returned
13 | SparkFun Logic Level Converter (Bi-Directional) | 1 | SparkFun | BOB-12009 | In use | 2026-03-03 | New | Used for project
14 | 18650 Rechargeable Li-ion Batteries (3500mAh each) | 4 | IMR Batteries | INR18650-35E | In use | 2026-02-27 | New | Used for project
15 | Inline Fuse Holders with Fuses (various ratings) | 1 | Amazon | B07D3QKF5S | Station 9, Box 5 | 2026-03-03 | New | Not Used, not returned
16 | Pi Switch (for safe shutdown) | 1 | PiShop.us | Pi-Supply-Switch | Station 9, Box 5 | 2026-02-27 | New | Not Used, not returned
17 | Jumper Wires (Female-to-Male, 8-inch) | 1 | Amazon | B01LZF1ZSZ | In use, extras in Station 9, Box 5 | 2026-02-27 | New
18 | 26-pin GPIO male to female extension for Raspberry Pi | 1 | Adafruit | 2101 | Station 9, Box 2 | 2026-02-27 | New | Not Used, not returned
19 | 26-pin GPIO Ribbon Cable for Raspberry Pi | 1 | Adafruit | 862 | Station 9, Box 2 | 2026-02-27 | New | Not Used, not returned
20 | USB A to Mini-B cable (power/programming for Arduino Nano) | 1 | Amazon | B09DCLRYH6 | One used, other in Station 9, Box 1 | 2026-03-03 | New | One Used, One not used, not returned
21 | Grove Electromagnet | 1 | Mouser | 713-101020073 | Station 9, Box 4 | 2026-02-27 | New | Not Used, not returned
22 | Nema 17 Stepper Motor | 2 | Adafruit | 324 | In use | 2026-03-03 | New | Used for project
23 | GT2 Timing Belt, 10 m (6 mm width, 2 mm pitch) | 1 | Amazon | 3DP AMZN-10160 | In use, leftover belt in Station 9, Box 4 | 2026-02-27 | New | Used for project
24 | GT2 Belt Pulley (16-tooth) | 2 | McMaster-Carr | 3684N12 | In use | 2026-02-27 | New | Used for project
25 | Idler Pulley, Aluminum | 1 | Amazon | B07RV2T54M | In use, extras in Station 9, Box 4 | 2026-02-27 | New | Used for project
26 | 3D Printer Rollers | 1 | Amazon | ‎B08B4JDB67 | In use, extras in Station 9, Box 4 | 2026-02-27 | New | Used for project
27 | Aluminum Extrusion Kit (2020 T-slot, 4x1220 mm) | 1 | Amazon | B0CLGX27MY | In use, extras in Station 9, Box 4 | 2026-02-27 | New | Used for project
28 | 2020 Aluminum Extrusion Corner Bracket Kit | 1 | Amazon | B0FLD88X6Y | In use, extras in Station 9, Box 4 | 2026-02-27 | New | Used for project
29 | 3.5 inch LCD Screen | 1 | Amazon | B0BJDTL9J3 | Capstone Lab West Side Closet | 2026-03-03 | New | Not Used, damaged
30 | Mounted USB Coupler | 1 | Amazon | B0DT4D13CK | Station 9, Box | 2026-03-03 | New | Used for project
31 | USB Microphone | 1 | Amazon | B08ZQSCJS3 | In use, case in Station 9, Box 3 | 2026-02-27 | New | Used for project
32 | 3/4 inch x 2 ft x 4 ft Plywood (Sides) | 1 | Lowe's | 6654 | In use | 2026-03-06 | New | Used for project
33 | 1/2 inch x 4 foot x 8 foot Plywood (Bottom) | 1 | Lowe's | 786167 | In use, scrap wood propped against Station 9/10 | 2026-03-06 | New | Used for project, leftover in Capstone Lab
34 | 30 1" Steel Fender Washers | 2 | Lowe's | 2215 | Station 9, Box 3 | 2026-03-06 | New | Not Used, not returned
35 | 1 1/2 in. Drywall Screws, 50ct | 1 | Lowe's | 68135 | Station 9, Box 3 | 2026-03-06 | New | Used for project
36 | 5mm - 0.8 x 20-mm Phillips -Drive Machine screws | 2 | Lowe's | 999994844 | In use, extras in Station 9, Box 4 | 2026-03-06 | New | Used for project
37 | 5mm x 0.8 Zinc-plated Steel Hex Nut | 1 | Lowe's | able | In use, extras in Station 9, Box 4 | 2026-03-06 | New | Used for project
38 | 3mm - 0.5 x 10-mm Phillips -Drive Machine screws | 1 | Lowe's | 999994826 | In use, extras in Station 9, Box 4 | 2026-03-06 | New | Used for project
39 | Screws 1.6mm | 1 | Amazon | B0192PBLX8 | In use, extras in Station 9, Box 1 | 2026-03-25 | New | Used for project
40 | Quick Blow Glass Tube Fuse | 1 | Amazon | B07YC5ZTMV | In use, extras in Station 9, Box 5 | 2026-03-25 | New | Used for project
41 | Inline Screw Type Fuse Holder | 2 | Amazon | B07SPS14WX | Station 9, Box 5 | 2026-03-25 | New | Not Used, not returned
42 | Inline Screw Type Fuse Holder | 2 | Amazon | B07SN9RG2Q | In use, extras in Station 9, Box 5 | 2026-03-25 | New | Used for project
43 | Inline Fuse Holder 12V | 2 | Amazon | B0D7D25G62 | Station 9, Box 5 | 2026-03-25 | New | Not Used, not returned
44 | LCD Screen | 1 | Amazon | B0B1MK3SQ2 | In use, leftover cables in Station 9, Box 2 | 2026-03-25 | New | Used for project
45 | Uart cable for rpi | 1 | Digikey | 1568-CAB-28698-ND | In use | 2026-03-25 | New | Used for project
46 | Felt Pads | 1 | Amazon | B0FN41J1D5 | In use, extras in Station 9, Box 3 | 2026-03-25 | New | Used for project
47 | Wood Glue | 1 | Amazon | B0006U20NY | Station 9, Box 3 | 2026-03-25 | New | Not used, substituted for glue in Jeff's shop
48 | Standalone Electromagnet |  | Digikey | 1528-2689-ND | In use | 2026-03-30 | New | Used for project
49 | 40mm Fans | 1 | Amazon | B08ZY7X4CR | In use | 2026-04-09 | New | Used for project
50 | Raspberry Pi 5 | 1 | PiShop.us | SC1111 | In use | 2026-04-22 | New | Used for project
51 | Neodymium Magnets (to put in base of each piece) | 1 | Amazon | D03125H0125 | In use, extras in Station 9, Box 4 | 2026-04-22 | New | Used for project
52 | Acrylic Sheet | 2 | Dr. Van Neste's Lab | N/A | In use, extras returned to Dr. Van Neste's Lab | 2026-04-08 | Used | Used for project
53 | Mini HDMI to HDMI Cable | 1 | Capstone Lab | N/A | In use | 2026-04-08 | Used | Used for project
54 | Raspberry Pi Active Cooler | 1 | PiShop.us | SC1148 | In use | 2026-04-22 | New | Used for project
55 | Pin Headers | 1 | Dr. Van Neste's Lab | N/A | Half used, rest in Station 9, Box 2 | 2026-04-08 | Used | Used for project

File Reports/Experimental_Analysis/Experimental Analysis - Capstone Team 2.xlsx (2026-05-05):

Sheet: Power Tests
# Experimental Analysis for Power_PSU Section - Excel Ready Tables
---
**1. Voltage Regulation and Ripple Test**
**Purpose:**
This experiment measures the following criteria from the Detailed Design PSU and Power Tree (Detailed_Design_PSU.md, Power_Tree.md, and Power_Budget.md):
- The PSU shall provide a stable **5V DC rail** (up to 5 A) with ripple <5%.
- The **12V rail** (via MT3608 step-up) shall remain stable up to 1 A for stepper motors.
- The **3.3V sub-rail** (via Adafruit buck converter) shall remain stable.
- All rails must stay within ±5% of nominal voltage under no-load, average-load (~15.2 W input), and peak-load (~24.4 W input) conditions as defined in the power tree and budget breakdowns.
**Procedure:**
a. Power the system via the Raspberry Pi wall charger (SC0510) with fully charged 4×18650 batteries in the DFRobot UPS HAT.
b. Use a calibrated digital oscilloscope (or logic analyzer with voltage measurement) and multimeter to probe the 5V rail (direct UPS output), 12V rail (MT3608 output), and 3.3V rail (buck converter output).
c. Run the system through four operating states: -1 idle/sleep, -2 typical chess move (stepper motors + electromagnet active), -3 peak simultaneous load (RPi processing + motors + electromagnet), -4 battery-only mode.
d. Record steady-state DC voltage and peak-to-peak ripple for at least 30 seconds per state.
e. Repeat with wall power disconnected (UPS battery mode).
**Data Collection**
| | Trial | Number | | | Operating State |  | | | Power | | | Source | | | 5V | Avg | (V) | | | 5V | Ripple | p-p | (mV) | | | 12V | Avg | (V) | | | 12V | Ripple | p-p | (mV) | | | 3.3V | Avg | (V) | | | 3.3V | Ripple | p-p | (mV) | | | Min | Voltage | (V) | | | Max | Voltage | (V) | | | Notes

| | 1
| | 2
| | 3
| | 4
| | 5
**Trials:** There will be 5 trials per operating state (N ≥ 20 total trials).
**Biases:** Each trial will use freshly calibrated instruments; ambient temperature will be controlled (68–77°F); load states will be randomized; different team members will perform measurements.
---
**2. Power Consumption and Budget Verification Test**
**Purpose:**
This experiment verifies the power tree and budget calculations (Power_Budget.md).
**Data Collection**
| | Trial | Number | | | Test | | | Mode | | | Input | Power | (W) | | | Input | Current | (A) | | | 5V | Rail | Power | (W) | | | 12V | Rail | Power | (W) | | | 3.3V | Rail | Power | (W) | | | UPS | Efficiency | (%) | | | MT3608 | Efficiency | (%) | | | Notes

| | 1
| | 2
| | 3
**Trials:** 3 full gameplay-cycle trials + 2 peak-load trials (N ≥ 5 total).
---
**3. Battery Runtime and UPS Switching Latency Test**
**Purpose:**
This experiment measures battery runtime, UPS switchover latency, and sleep-mode power draw.
**Data Collection**
| | Trial | Number | | | Test | | | Type | | | Runtime | (min:sec) | | | UPS | Switch | Latency | (ms) | | | Sleep | Mode | Power | (W) | | | Total | Energy | Delivered | (Wh) | | | Pass/Fail | | | Notes

| | 1
| | 2
| | 3
| | 4
**Trials:** 1 full runtime trials and 10 UPS switch trials (N ≥ 13 total).
---
**4. Thermal Performance and Surface Temperature Test**
**Purpose:**
Verify external surface temperature ≤104°F (40°C) during continuous peak-load operation.
**Data Collection**
| | Trial | Number | | | Time | (min) | | | UPS | HAT | (°F) | | | MT3608 | (°F) | | | Battery | Pack | (°F) | | | Enclosure | Surface | (°F) | | | Ambient | (°F) | | | Max | Temp | (°F) | | | Pass/Fail | | | Notes

| | 1
| | 2
| | 3
**Trials:** 3 trials
---
**Component Inventory Tracking**
**Data Collection (copy-paste this table into Excel):**
| | Item | # | | | Description | | | Quantity | | | Vendor | | | Order | # | | | Storage | Location | | | Date | Acquired | | | Condition | | | Notes

| | 1
| | 2
| | 3
| | 4
| | 5
| | 6
| | 7
| | 8
| | 9
| | 10
---
**Summary**
These experiments directly validate the power detailed design, power tree distribution, component breakdowns, efficiency targets, protections, and runtime/safety specifications. Results will be analyzed in the full report with tables, scope screenshots, and comparisons to expected values.
---

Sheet: Thermal
Trial | Time (min) | Arduino | Temperature | Pass/Fail
1 | 10 | Motor A | 83.1
2 | 20 | Motor A | 85.8
3 | 30 | Motor A | 86.3
1 | 10 | Motor B | 86.1
2 | 20 | Motor B | 86.5
3 | 30 | Motor B | 86.3
1 | 10 | Stepper Driver A | 76.2
2 | 20 | Stepper Driver A | 74.8
3 | 30 | Stepper Driver A | 74.8
1 | 10 | Stepper Driver B | 75.3
2 | 20 | Stepper Driver B | 73.9
3 | 30 | Stepper Driver B | 73
1 | 10 | Mosfet | 76.8
2 | 20 | Mosfet | 73.5
3 | 30 | Mosfet | 74.3
1 | 10 | Flyback Diode | 75.7
2 | 20 | Flyback Diode | 73.2
3 | 30 | Flyback Diode | 72.8
1 | 10 | Arduino | 77
2 | 20 | Arduino | 75 |  | 1st 10 min normal game 2P
3 | 30 | Arduino | 74.1 |  | 2nd 10 min simple slow moves 2P
1 | 10 | Electromagnet | 76.6 |  | 3rd 10 min intense moves with ai
2 | 20 | Electromagnet | 74.1
3 | 30 | Electromagnet | 73.7
1 | 10 | Raspberry Pi | 107
2 | 20 | Raspberry Pi | 104.5
3 | 30 | Raspberry Pi | 101.6
1 | 10 | Screen (back surface) | 93.5
2 | 20 | Screen (back surface) | 94.2
3 | 30 | Screen (back surface) | 92.6
1 | 10 | UPS | 91.4
2 | 20 | UPS | 96.8
3 | 30 | UPS | 89.6
1 | 10 | Battery Pack | 78.6
2 | 20 | Battery Pack | 80.4
3 | 30 | Battery Pack | 75.9
1 | 10 | UPS/Pi Mount | 77.5
2 | 20 | UPS/Pi Mount | 78.3
3 | 30 | UPS/Pi Mount | 85.1
1 | 10 | Booster 1 | 78
2 | 20 | Booster 1 | 75
3 | 30 | Booster 1 | 73.5
1 | 10 | Booster 2 | 78.2
2 | 20 | Booster 2 | 76.6
3 | 30 | Booster 2 | 75.3
1 | 10 | (Acryllic) Board Surface | 77
2 | 20 | (Acryllic) Board Surface | 75
3 | 30 | (Acryllic) Board Surface | 71.9

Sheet: UART Reliability
Trial Num | Expected source square | Expected destination square | Actual destination square observed | Piece moved correctly (Y/N) | ACK/NACK/timeout received
1 | E2 | E4 | E4 | Y | ACK
2 | E7 | E5 | E5 | Y | ACK
3 | B1 | C3 | C3 | Y | ACK
4 | G8 | F6 | F6 | Y | ACK
5 | F2 | F4 | F4 | Y | ACK
6 | F4 | capture area | capture area | Y | ACK
6 | E5 | F4 | F4 | Y | ACK
7 | E4 | E5 | E5 | Y | ACK
8 | F6 | G8 | G8 | Y | ACK
9 | G1 | F3 | F3 | Y | ACK
10 | D7 | D6 | D6 | Y | ACK
11 | D2 | D4 | D4 | Y | ACK
12 | E5 | captured | Capture area | Y | ACK
13 | D6 | E5 | E5 | Y | ACK
14 | D4 | D2 | D2 | Y | ACK
15 | E5 | E7 | E7 | Y | ACK
16 | C3 | B1 | B1 | Y | ACK
17 | F3 | G1 | G1 | Y | ACK
18 | F4 | D7 | D7 | Y | ACK
19 | captured | E2 | E2 | Y | ACK
20 | captured | F2 | F2 | Y | Timeout | This probably means that Arduino recieved move and moved correctly but did not send back an ACK or NACK

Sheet: Speech Recognition Accuracy
Trial Number | Speaker Name | Command | Recognized | Correct
 | Example | move a3b3 | Y | N |  | List of commands: |  |  | needs to be this distance away from the microphone:
1 | Jack | Chess Two | Y | Y |  | Chess Two |  |  | 25 inches
2 | Jack | move b2b4 | Y | Y |  | move b2b4 |  |  | medium speaking voice
3 | Jack | move c7c5 | Y | Y |  | move c five |  |  | recognized Y means recognized on first try
4 | Jack | move d2d4 | Y | Y |  | move d2d4 |  |  | correct Y means correct after being recognized
5 | Jack | move b8a6 | Y | Y |  | move knight a six |  |  | loud fan was turned off after Allison trial 4
6 | Jack | move c2c4 | Y | Y |  | move c2c4
7 | Jack | move d8a5 | Y | Y |  | move queen a five
8 | Jack | move d1d3 | Y | Y |  | move d1d3
9 | Jack | move g8h6 | Y | Y |  | move knight h six
10 | Jack | move c1e3 | Y | Y |  | move bishop e three
11 | Jack | move h6f5 | Y | Y |  | move h6f5
12 | Jack | move b1c3 | Y | Y |  | move b1c3
13 | Jack | move c5d4 | Y | Y |  | move c takes d four
14 | Jack | move castle | Y | Y |  | move castle
15 | Jack | move e7e5 | Y | Y |  | move e7e5
16 | Jack | move g1f3 | Y | Y |  | move knight f three
17 | Jack | move a5d5 | Y | Y |  | move queen d five
18 | Jack | move e3h6 | Y | N |  | move e3h6
19 | Jack | chess resign | Y | Y |  | chess resign
20 | Jack | chess yes | Y | Y |  | chess yes
1 | Allison | Chess Two | Y | Y
2 | Allison | move b2b4 | Y | Y
3 | Allison | move c7c5 | N | Y
4 | Allison | move d2d4 | N | Y
5 | Allison | move b8a6 | Y | Y
6 | Allison | move c2c4 | Y | Y
7 | Allison | move d8a5 | Y | Y
8 | Allison | move d1d3 | Y | Y
9 | Allison | move g8h6 | Y | Y
10 | Allison | move c1e3 | Y | Y
11 | Allison | move h6f5 | Y | Y
12 | Allison | move b1c3 | Y | Y
13 | Allison | move c5d4 | N | Y
14 | Allison | move castle | N | Y
15 | Allison | move e7e5 | Y | Y
16 | Allison | move g1f3 | Y | Y
17 | Allison | move a5d5 | Y | Y
18 | Allison | move e3h6 | Y | N
19 | Allison | chess resign | Y | Y
20 | Allison | chess yes | Y | Y
1 | Noah | Chess Two | y | y
2 | Noah | move b2b4 | y | y
3 | Noah | move c7c5 | y | y
4 | Noah | move d2d4 | y | y
5 | Noah | move b8a6 | y | y
6 | Noah | move c2c4 | y | y
7 | Noah | move d8a5 | y | y
8 | Noah | move d1d3 | y | y
9 | Noah | move g8h6 | y | y
10 | Noah | move c1e3 | y | y
11 | Noah | move h6f5 | y | y
12 | Noah | move b1c3 | y | y
13 | Noah | move c5d4 | y | y
14 | Noah | move castle | y | y
15 | Noah | move e7e5 | y | y
16 | Noah | move g1f3 | y | y
17 | Noah | move a5d5 | y | y
18 | Noah | move e3h6 | Y | N
19 | Noah | chess resign | y | y
20 | Noah | chess yes | Y | Y | This and before is old data
1 | Lewis | Chess Two | Y | Y
2 | Lewis | move b2b4 | Y | Y
3 | Lewis | move c five | Y | Y |  |  |  | Command heard first time | Command heard correctly after being heard first time
4 | Lewis | move d2d4 | Y | Y |  |  | Lewis | 100.00% | 94.00%
5 | Lewis | move knight a six | Y | Y |  |  | Nathan | 90.00% | 85.00%
6 | Lewis | move c2c4 | Y | Y |  |  | Jack | 100.00% | 100.00%
7 | Lewis | move queen a five | Y | Y |  |  | Allison | 100.00% | 90.00%
8 | Lewis | move d1d3 | Y | Y |  |  | Noah | 95.00% | 100.00%
9 | Lewis | move knight h six | Y | Y
10 | Lewis | move bishop e three | Y | Y |  |  | Total | 97.00% | 100.00%
11 | Lewis | move h6f5 | Y | Y
12 | Lewis | move b1c3 | Y | Y
13 | Lewis | move c takes d four | Y | Y
14 | Lewis | move castle | Y | Y
15 | Lewis | move e7e5 | Y | Y
16 | Lewis | move knight f three | Y | Y
17 | Lewis | move queen d five | Y | Y
18 | Lewis | move e3h6 | Y | Y
19 | Lewis | chess resign | Y | Y
20 | Lewis | chess yes | Y | Y
1 | Nathan | Chess Two | Y | Y
2 | Nathan | move b2b4 | Y | N
3 | Nathan | move c five | Y | Y
4 | Nathan | move d2d4 | Y | N
5 | Nathan | move knight a six | Y | Y
6 | Nathan | move c2c4 | N | Y
7 | Nathan | move queen a five | Y | N | NOTE AT START till trial 7 there was additional noise pollution due to lab being busy/noisy
8 | Nathan | move d1d3 | Y | Y
9 | Nathan | move knight h six | Y | Y
10 | Nathan | move bishop e three | Y | Y
11 | Nathan | move h6f5 | Y | Y
12 | Nathan | move b1c3 | Y | Y
13 | Nathan | move c takes d four | Y | Y
14 | Nathan | move castle | Y | Y
15 | Nathan | move e7e5 | Y | Y
16 | Nathan | move knight f three | Y | Y
17 | Nathan | move queen d five | Y | Y
18 | Nathan | move e3h6 | Y | Y
19 | Nathan | chess resign | Y | Y
20 | Nathan | chess yes | N | Y
1 | Jack | Chess Two | Y | Y
2 | Jack | move b2b4 | Y | Y
3 | Jack | move c five | Y | Y
4 | Jack | move d2d4 | Y | Y
5 | Jack | move knight a six | Y | Y
6 | Jack | move c2c4 | Y | Y
7 | Jack | move queen a five | Y | Y
8 | Jack | move d1d3 | Y | Y
9 | Jack | move knight h six | Y | Y
10 | Jack | move bishop e three | Y | Y
11 | Jack | move h6f5 | Y | Y
12 | Jack | move b1c3 | Y | Y
13 | Jack | move c takes d four | Y | Y
14 | Jack | move castle | Y | Y
15 | Jack | move e7e5 | Y | Y
16 | Jack | move knight f three | Y | Y
17 | Jack | move queen d five | Y | Y
18 | Jack | move e3h6 | Y | Y
19 | Jack | chess resign | Y | Y
20 | Jack | chess yes | Y | Y
1 | Allison | Chess Two | Y | Y
2 | Allison | move b2b4 | Y | Y
3 | Allison | move c five | Y | Y
4 | Allison | move d2d4 | Y | Y
5 | Allison | move knight a six | Y | Y
6 | Allison | move c2c4 | Y | Y
7 | Allison | move queen a five | Y | Y
8 | Allison | move d1d3 | Y | Y
9 | Allison | move knight h six | Y | N
10 | Allison | move bishop e three | Y | N
11 | Allison | move h6f5 | Y | Y
12 | Allison | move b1c3 | Y | Y
13 | Allison | move c takes d four | Y | Y
14 | Allison | move castle | Y | Y
15 | Allison | move e7e5 | Y | Y
16 | Allison | move knight f three | Y | Y
17 | Allison | move queen d five | Y | Y
18 | Allison | move e3h6 | Y | Y
19 | Allison | chess resign | Y | Y
20 | Allison | chess yes | Y | Y
1 | Noah | Chess Two | Y | Y
2 | Noah | move b2b4 | Y | Y
3 | Noah | move c five | Y | Y
4 | Noah | move d2d4 | Y | Y
5 | Noah | move knight a six | Y | Y
6 | Noah | move c2c4 | Y | Y
7 | Noah | move queen a five | Y | Y
8 | Noah | move d1d3 | N | Y
9 | Noah | move knight h six | Y | Y
10 | Noah | move bishop e three | Y | Y
11 | Noah | move h6f5 | Y | Y
12 | Noah | move b1c3 | Y | Y
13 | Noah | move c takes d four | Y | Y
14 | Noah | move castle | Y | Y
15 | Noah | move e7e5 | Y | Y
16 | Noah | move knight f three | Y | Y
17 | Noah | move queen d five | Y | Y
18 | Noah | move e3h6 | Y | Y
19 | Noah | chess resign | Y | Y
20 | Noah | chess yes | Y | Y

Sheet: Move Validation
Trial Number | Command | Expected: Illegal(i)/legal(L) | Result: Correct(Y) False (N)
Example | a1a3 | L | N
1 | c2c4 | L | Y
2 | f3f5 | i | Y
3 | h7h5 | L | Y
4 | g1f4 | i | Y
5 | g1f3 | L | Y
6 | h1h7 | i | Y
7 | h8h6 | L | Y
8 | c1c3 | i | Y
9 | b1a3 | L | Y
10 | f3d4 | i | Y
11 | h6d6 | L | Y
12 | d6d4 | i | Y
13 | d1a4 | L | Y
14 | h1h1 | i | Y
15 | d6d4 | L | Y
16 | castle | i | Y
17 | d2d3 | L | Y
18 | h5g4 | i | Y
19 | h5h4 | L | Y
20 | f1g8 | i | Y
21 | c1d2 | L | Y
22 | d4c5 | i | Y
23 | d4c4 | L | Y
24 | castle | i | Y
25 | d2c3 | L | Y
26 | b8a5 | i | Y
27 | b8a6 | L | Y
28 | e7e5 | i | Y
29 | castle | L | Y
30 | d4a3 | i | Y
31 | c4a4 | L | Y
32 | c1a1 | i | Y
33 | c1d2 | L | Y
34 | e2e5 | i | Y
35 | a4a3 | L | Y
36 | g2f1 | i | Y
37 | g2g4 | L | Y
38 | h4h2 | i | Y
39 | h4g3 (enpassant) | L | Y
40 | a1a8 | i | Y

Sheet: Processing Latency
Trial Number | Time from voice to display in seconds | Command | Illegal(i)/legal(L)
Example | 1.2 | a1a3 | i
1 | 1.06 | c2c4 | L
2 | 1.01 | f3f5 | i
3 | 1.16 | h7h5 | L
4 | 0.98 | g1f4 | i
5 | 1.03 | g1f3 | L
6 | 0.84 | h1h7 | i
7 | 0.97 | h8h6 | L
8 | 1.41 | c1c3 | i
9 | 0.96 | b1a3 | L
10 | 1.08 | f3d4 | i
11 | 1.21 | h6d6 | L
12 | 1.16 | d6d4 | i
13 | 0.95 | d1a4 | L
14 | 0.61 | h1h1 | i
15 | 0.88 | d6d4 | L
16 | 1.04 | castle | i
17 | 1.18 | d2d3 | L
18 | 0.95 | h5g4 | i
19 | 1.1 | h5h4 | L
20 | 0.8 | f1g8 | i
21 | 0.68 | c1d2 | L
22 | 1.06 | d4c5 | i
23 | 1.25 | d4c4 | L
24 | 0.93 | castle | i
25 | 1.01 | d2c3 | L
26 | 1.06 | b8a5 | i
27 | 0.96 | b8a6 | L
28 | 0.91 | e7e5 | i
29 | 1.11 | castle | L
30 | 0.85 | d4a3 | i
31 | 0.71 | c4a4 | L
32 | 0.96 | c1a1 | i
33 | 0.81 | c1d2 | L
34 | 0.88 | e2e5 | i
35 | 0.81 | a4a3 | L
36 | 0.88 | g2f1 | i
37 | 0.76 | g2g4 | L
38 | 0.84 | h4h2 | i
39 | 1.01 | h4g3 (enpassant) | L
40 | 0.98 | a1a8 | i

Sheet: Move Completion Time
Trial Number | Move Type | Move | Time (sec)
Ex:
1 |  | a1a2 | 5.58
2 |  | a1a4 | 8.13
3 |  | a1a8 | 12.86
4 |  | a1c3 | 9.3
5 |  | a1h8 | 22.04
6 |  | a1b3 | 11.21
7 |  | a1a11 | 7.94
8 |  | h8a11 | 30
9 |  | a1a11 | 8.34
10 |  | a8a1 | 12.63

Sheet: Boot Noise
Boot Noise Rejection
Trial Number | Boot Movement | Start Command Received | Valid Move Executed | Pass/Fail
1 | No | Yes | Yes | Pass
2 | No | Yes | Yes | Pass
3 | No | Yes | Yes | Pass

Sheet: Edge Boundary
Move | Source | Actual Destination | Boundary Tested | Within Bounds (y/n)
a1a8 | a1 | a8 | X left | Y
h1h8 | h1 | h8 | X right | Y
a1a11 | a1 | a11 | Y bottom | Y
h8h10 | h8 | h10 | Y top | Y

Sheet: Electromagnet Switching
Trial Number | Turn-On Latency (µs) | Turn-Off Latency (µs)
1 | 3 | 3
2 | 2.7 | 2.8
3 | 3 | 2.9
4 | 2.8 | 2.9
5 | 2.6 | 2.7
6 | 3 | 3
7 | 2.7 | 2.6
8 | 2.8 | 2.8
9 | 2.9 | 3
10 | 2.8 | 2.7
 | Mean: 2.83 | Mean: 2.84
 | Max: 3 | Max: 3

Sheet: Flyback Diode
Trial Number | On Duration (seconds) | Peak Spike (V) | Ambient Temperature (°F) | Pass/Fail
1 | 0.2 | 5 | 62 | Pass
2 | 1 | 5 | 62 | Pass
3 | 2 | 5 | 63 | Pass
4 | 5 | 5 | 62 | Pass

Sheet: Command Latency
Trial Number | Move | Move Type | Meaured Latency (µs) | Mean | Std Dev | Min | Max | Target Time
1 | Move A2A4 | Straight (startup) | 736 | 636.4 | 56.14837487 | 596 | 758 | <= 50ms
2 | Move A7A45 | Straight | 596
3 | Move B2B3 | Straight | 598
4 | Move B8A6 | L-move | 610
5 | Move C1A3 | Diagonal | 618
6 | Move B7B6 | Straight | 600
7 | Move H2H3 | Straight (startup) | 758
8 | Move G7G5 | Straight | 608
9 | Move H1H3 | Straight | 618
10 | Move G8F6 | L-move | 622

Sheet: Compliance
Category | Checklist Item | Severity | Result | Score | Total Score | Critical Fail Count | Final Result | Notes: Class 2
Circuit Classification | Circuit correctly classified (Class 1/2/3) | Critical | Pass | 0 | 3 | 0 | PASS
Circuit Classification | Power source matches classification | Critical | Pass | 0
Overcurrent Protection | Protection device present (if required) | Critical | Pass | 0
Overcurrent Protection | Protection rating appropriate | Major | Pass | 0
Conductor Sizing | Wire gauge appropriate for load | Major | Pass | 0
Insulation | Insulation rating ≥ operating voltage | Critical | Pass | 0
Insulation | No insulation damage | Critical | Pass | 0
Installation Method | Approved wiring method used | Major | Pass | 0
Installation Method | Conductors protected from damage | Major | Pass | 0
Installation Method | Proper separation maintained | Major | Pass | 0
Grounding | Common DC ground reference across all subsystems | Critical | Pass | 0
Grounding | Ground connections secure | Critical | Pass | 0
Grounding | Continuity verified (multimeter) | Critical | Pass | 0
Flexible Cords | Proper cord type used | Major | Pass | 0
Flexible Cords | Strain relief present | Major | Fail | 3
Flexible Cords | No cord damage | Critical | Pass | 0
Equipment/Enclosure | No exposed live parts | Critical | Pass | 0
Equipment/Enclosure | Enclosure secured | Major | Pass | 0
Safety Labeling | Warning labels present | Minor | Pass | 0
Safety Labeling | Labels legible | Minor | Pass | 0
Accessibility | No tripping hazards | Minor | Pass | 0
Accessibility | Adequate clearance | Minor | Pass | 0
Disconnects | Disconnect available (if required) | Critical | Pass | 0
Post-Modification | System rechecked after changes | Major | Pass | 0

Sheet: Run Switch Sleep
Trial | Runtime (min:sec) | Total Energy Delivered (Wh) | Pass / Fail
1 | 122:00:00 | ? | Pass | Notes from runtime: froze @ 34, fans plugged back in at 50, motion was not constant had to stop for freeze, also had to stop for retensioning, froze 1hr12, fans plugged in 1hr17, froze again 1hr17, battery 1 depleted around 41, battery 2 depleted around 1hr17, fans plugged in 1hr25, froze 1hr25, fans plugged in 1hr30, battery 3 depleted around 1hr34, froze 1hr42, fans plugged in 1hr46, Made it 2hr02 ended testing for allowance for more power testing
 |  |  |  | NOTE: when there is a long time between spoken commands I believe that vosk is getting into a bad internal state somehow and could possubly be fixed by restarting after hearing absolutely nothing for 15 seconds, this should be fine due to vosk constantly trying to hear words so if there is nothing there is a problem
Trial | Mid-Move? | Switchover Latency (ms) | Brownout? | Reboot? | Move Completed? | Halted / Recovered Cleanly? | Pass / Fail
1 | No | 0 | No | No | N/A | N/A | Pass
2 | Yes | 0 | No | No | Yes | Recovered Cleanly | Pass
3 | Yes | 0 | No | No | Yes | Recovered Cleanly | Pass
4 | Yes | 0 | No | No | Yes | Recovered Cleanly | Pass
5 | Yes | 0 | No | No | Yes | Recovered Cleanly | Pass
Trial | Sleep Power (W)
1 | 0.045W
2 | 0.044W

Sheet: Weight Portability
weight | 33.2 |  |  | Note: 18 ft 36 total
Trial | Team Member | Carry Completed? | Post Carry Damage? | Pass / Fail
1 | Nathan | Yes | No | Pass
2 | Jack | Yes | No | Pass
3 | Lewis | Yes | No | Pass
4 | Noah | Yes | No | Pass
5 | Allison | Yes | No | Pass

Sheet: Voltage Regulation, Ripple, and
Trial | Operating State | Power Source | 5V Avg (V) | 5V Ripple p-p (mV) | 12V Avg (V) | 12V Ripple p-p (mV) | 5V Min (V) | 5V Max (V) | 12V Min (V) | 12V Max (V) | <50 V? | Interference? | Notes
1 | 1 – Idle/Sleep | Wall & Battery | 5.02 | 110 | 12.15 | 180 | 4.96 | 5.08 | 12.05 | 12.25 | Yes | None | Expected
2 | 2 – Typical chess move | Wall & Battery | 4.95 | 240 | 11.95 | 320 | 4.83 | 5.07 | 11.8 | 12.15 | Yes | None | Expected
3 | 3 – Peak simultaneous load | Wall & Battery | 4.93 | 290 | 11.85 | 420 | 4.78 | 5.08 | 11.65 | 12.05 | Yes | None | Expected
4 | 4 – Battery-only mode | Battery | 4.98 | 180 | 12.05 | 250 | 4.89 | 5.07 | 11.9 | 12.2 | Yes | None | Expected
5 | 1 – Idle/Sleep | Wall & Battery | 5.01 | 105 | 12.18 | 175 | 4.95 | 5.07 | 12.08 | 12.28 | Yes | None | Expected
6 | 2 – Typical chess move | Wall & Battery | 4.96 | 235 | 11.92 | 310 | 4.84 | 5.08 | 11.77 | 12.07 | Yes | None | Expected
7 | 3 – Peak simultaneous load | Wall & Battery | 4.92 | 295 | 11.82 | 430 | 4.77 | 5.07 | 11.62 | 12.02 | Yes | None | Expected
8 | 4 – Battery-only mode | Battery | 4.97 | 185 | 12.02 | 255 | 4.88 | 5.06 | 11.87 | 12.17 | Yes | None | Expected
9 | 1 – Idle/Sleep | Wall & Battery | 5.03 | 115 | 12.12 | 185 | 4.97 | 5.09 | 12.02 | 12.22 | Yes | None | Expected
10 | 2 – Typical chess move | Wall & Battery | 4.94 | 245 | 11.9 | 330 | 4.82 | 5.06 | 11.75 | 12.05 | Yes | None | Expected
11 | 3 – Peak simultaneous load | Wall & Battery | 4.91 | 305 | 11.8 | 440 | 4.76 | 5.06 | 11.6 | 12 | Yes | None | Expected
12 | 4 – Battery-only mode | Battery | 4.99 | 175 | 12.08 | 245 | 4.9 | 5.08 | 11.93 | 12.23 | Yes | None | Expected

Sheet: Power Consumption and Budget Ve
Trial | Test / Mode | Input Power (W) | Input Current (A) | 5V Rail Power (W) | 12V Rail Power (W) | UPS Efficiency (%) | MT3608 Efficiency (%) | Notes
1 | Idle/Sleep | 6.5 | 0.28 | 3.8 | 1.2 | 92 | 88 | Low-draw sleep mode
2 | Typical gameplay | 15.8 | 0.68 | 8.5 | 5.5 | 89 | 85 | Mixed moves (average load)
3 | Peak simultaneous load | 23.5 | 1.02 | 11.5 | 9.8 | 87 | 82 | Motors + electromagnet + Pi max
4 | Full gameplay cycle | 16.2 | 0.7 | 8.8 | 5.7 | 88 | 84 | Long cycle (matches runtime test)
5 | Battery-only peak load | 22.8 | 1 | 11.2 | 9.5 | 86 | 81 | Wall unplugged

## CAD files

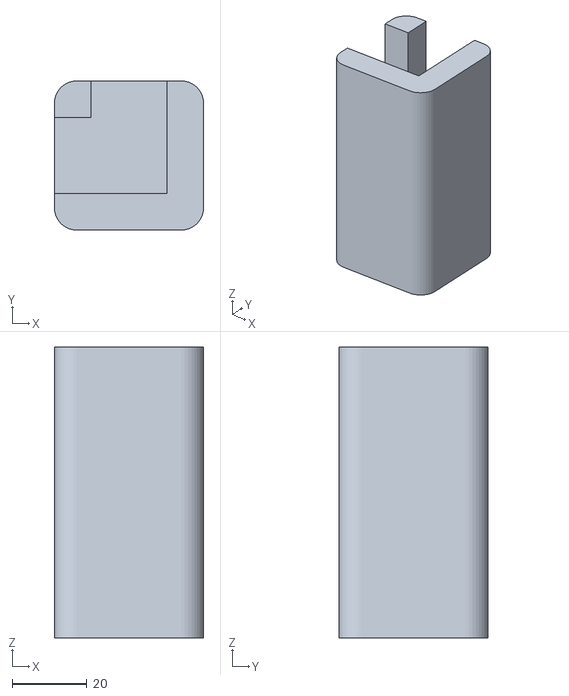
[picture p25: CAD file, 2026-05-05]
Documentation/3D Models/post_detailed_design_parts/corner_supports.STL
40.0 x 40.0 x 78.0

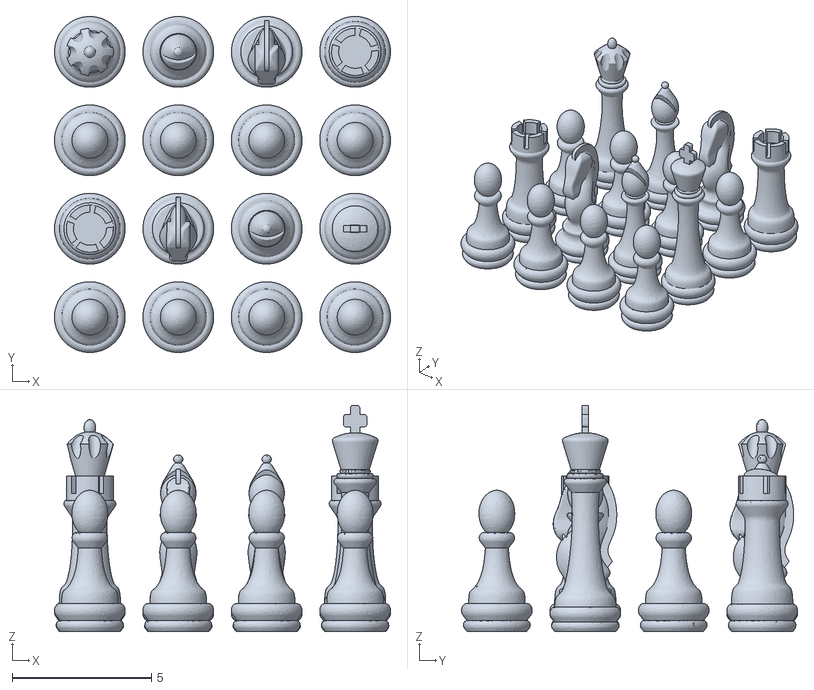
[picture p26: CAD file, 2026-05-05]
Documentation/3D Models/pre_detailed_design_parts/Chess Pieces.stl
12.1 x 12.1 x 8.13

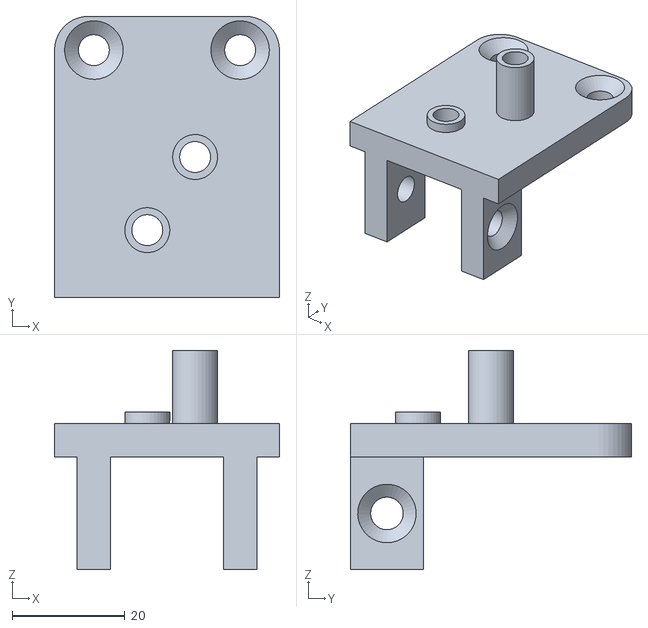
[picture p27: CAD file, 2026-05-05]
Documentation/3D Models/post_detailed_design_parts/trolly1.STL
40.0 x 50.0 x 39.0

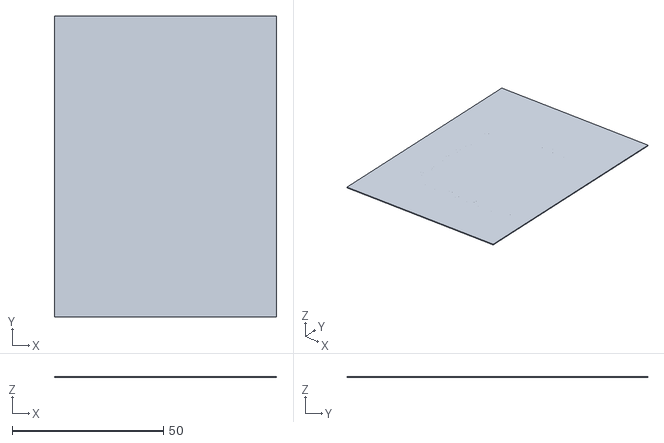
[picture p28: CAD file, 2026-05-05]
Documentation/3D Models/pre_detailed_design_parts/Automated Chess Board.stl
73.5 x 99.6 x 0.327

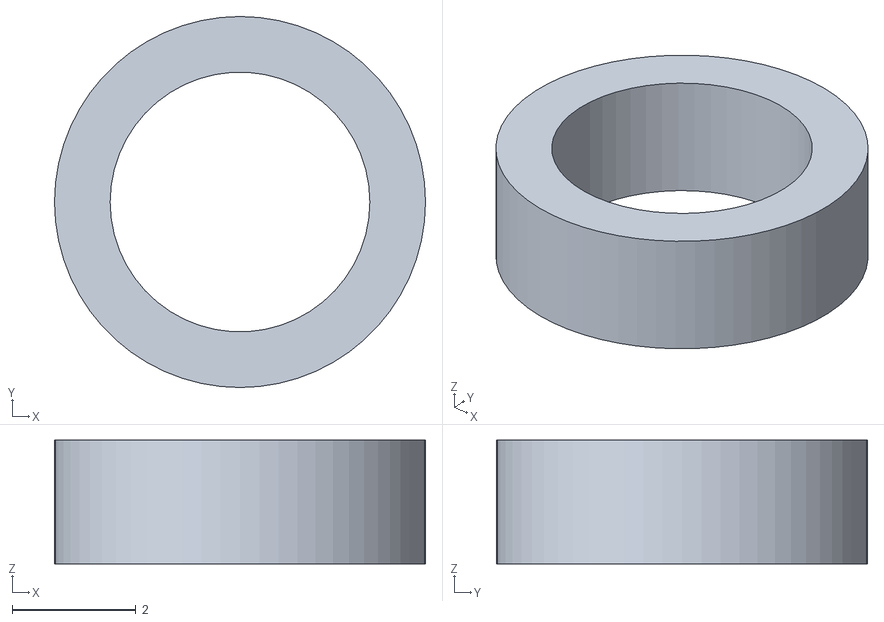
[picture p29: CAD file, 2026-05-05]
Documentation/3D Models/post_detailed_design_parts/spacer.STL
6.00 x 6.00 x 2.00

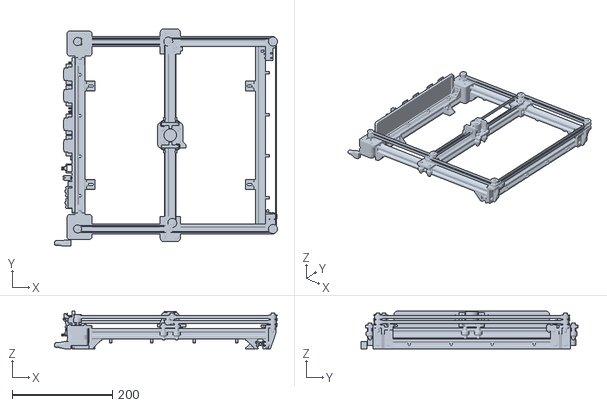
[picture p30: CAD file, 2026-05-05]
Documentation/3D Models/pre_detailed_design_parts/coreXY.STL
445.0 x 433.0 x 75.0

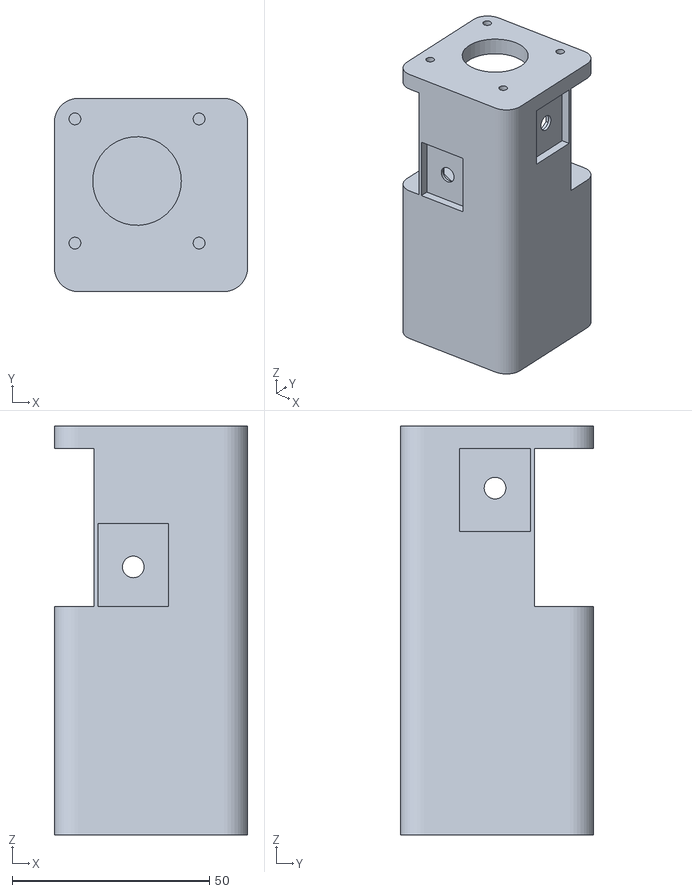
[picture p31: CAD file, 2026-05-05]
Documentation/3D Models/post_detailed_design_parts/motor2.STL
49.0 x 49.0 x 103.8

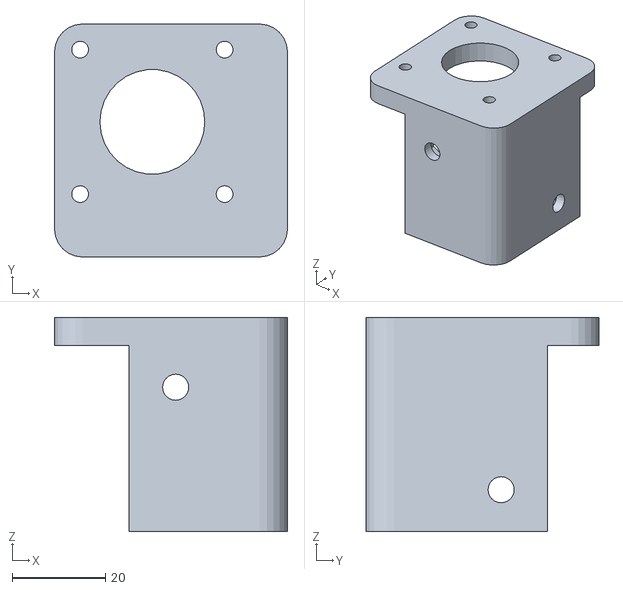
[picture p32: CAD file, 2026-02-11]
Documentation/3D Models/pre_detailed_design_parts/Motor_Support_A.stl
50.0 x 50.0 x 46.0

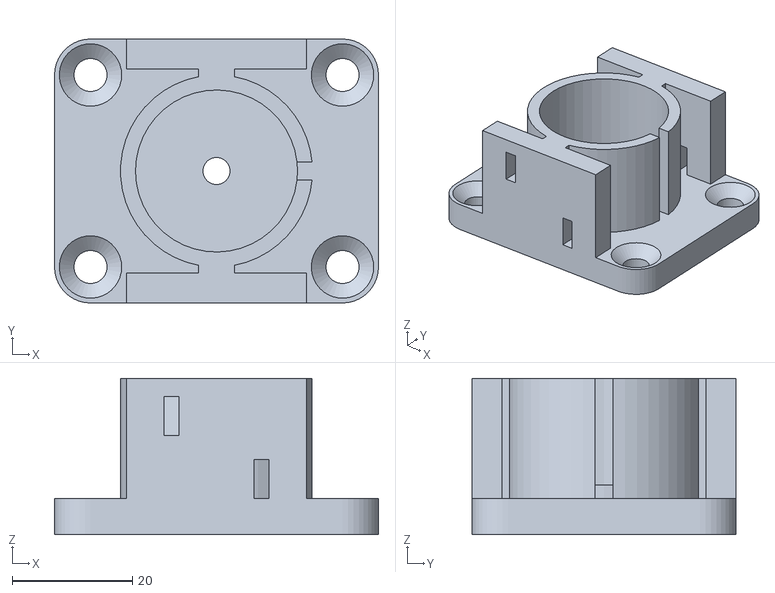
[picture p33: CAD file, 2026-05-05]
Documentation/3D Models/post_detailed_design_parts/em_support2.25.STL
54.0 x 44.0 x 26.0

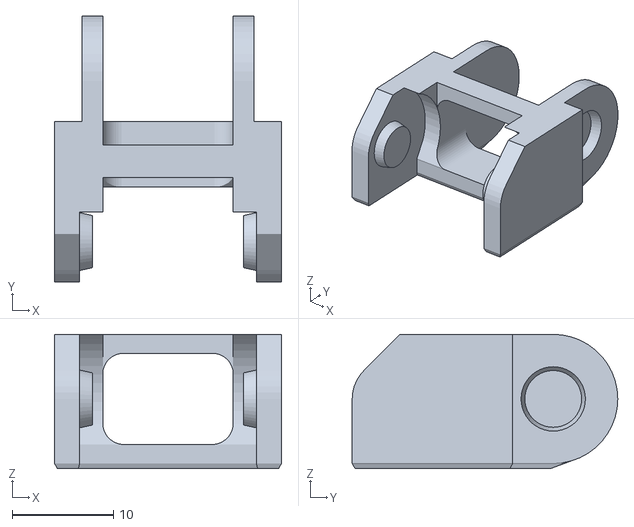
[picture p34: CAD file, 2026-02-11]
Documentation/3D Models/pre_detailed_design_parts/CableChain.stl
22.4 x 26.3 x 13.3

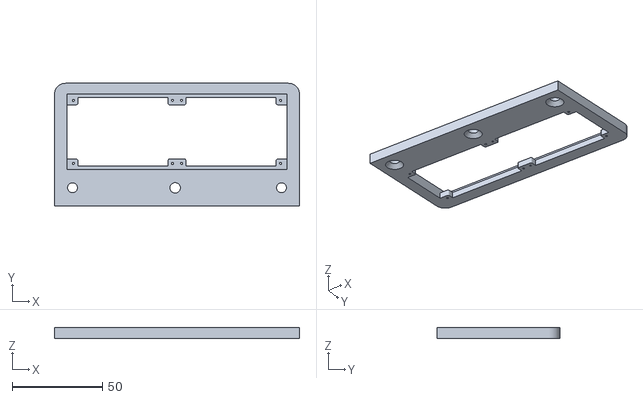
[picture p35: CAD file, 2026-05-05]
Documentation/3D Models/post_detailed_design_parts/bigbracket.STL
136.0 x 68.0 x 6.00

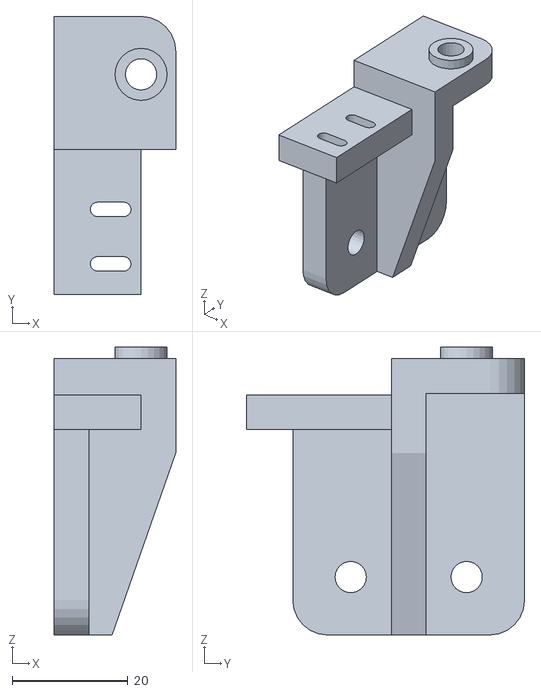
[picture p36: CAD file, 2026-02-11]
Documentation/3D Models/pre_detailed_design_parts/Pulley_Support_A.stl
21.0 x 48.0 x 49.7

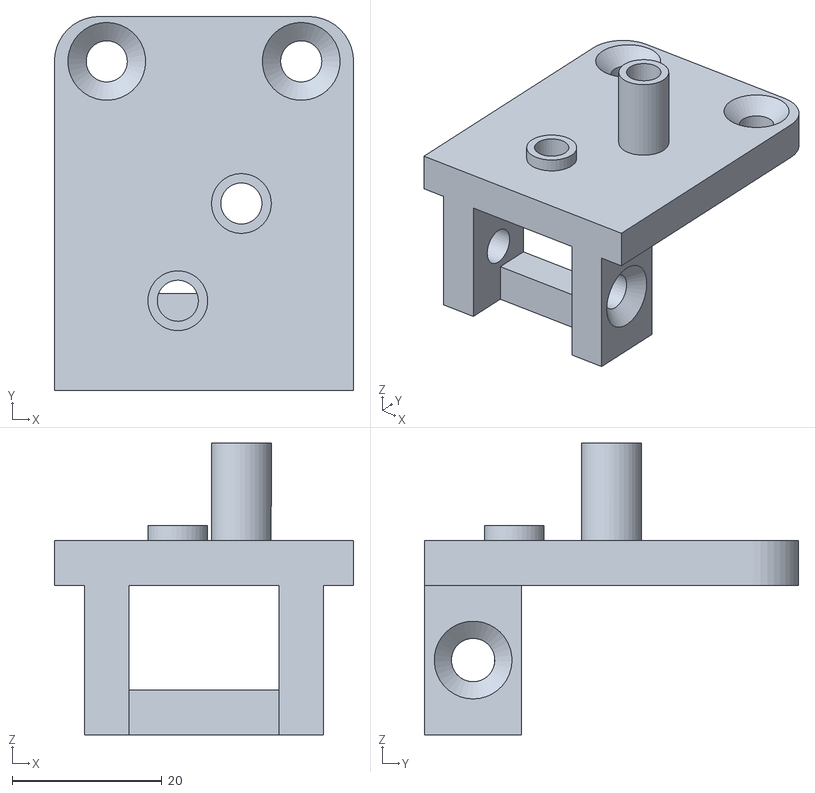
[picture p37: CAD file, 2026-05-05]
Documentation/3D Models/post_detailed_design_parts/trolly1mod.STL
40.0 x 50.0 x 39.0

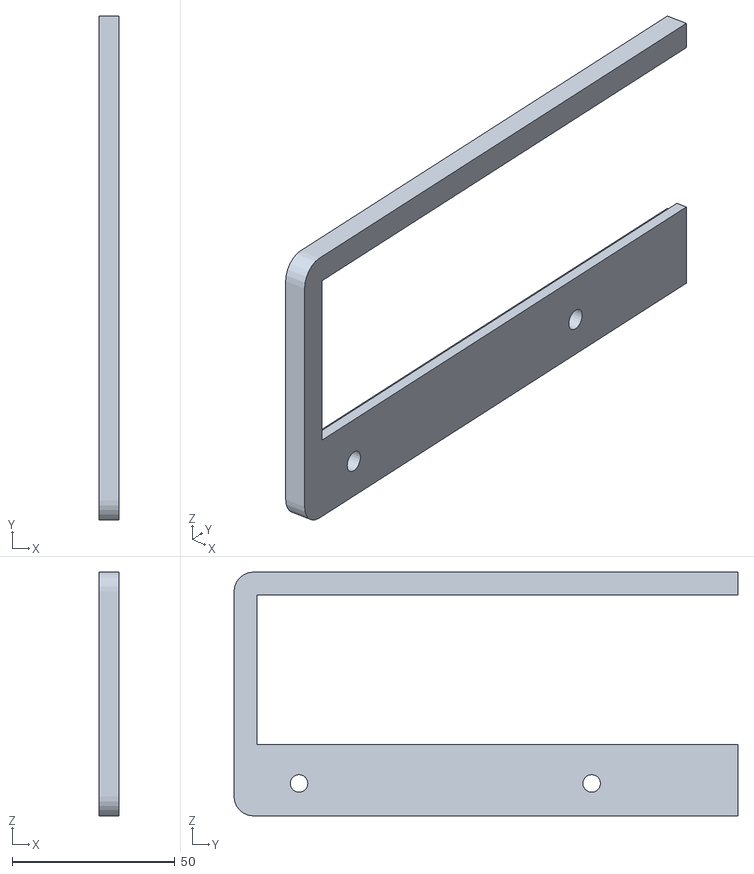
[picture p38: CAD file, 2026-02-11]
Documentation/3D Models/pre_detailed_design_parts/Electronic_Support_B.stl
6.00 x 155.0 x 75.0

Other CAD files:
Documentation/3D Models/post_detailed_design_parts/em_support2.5.STL
Documentation/3D Models/pre_detailed_design_parts/Electromagnet_Support.stl
Documentation/3D Models/post_detailed_design_parts/bracket.STL
Documentation/3D Models/pre_detailed_design_parts/Trolley_Support_B.stl
Documentation/3D Models/post_detailed_design_parts/em_support2.STL
Documentation/3D Models/post_detailed_design_parts/em_support3.STL
Documentation/3D Models/post_detailed_design_parts/motor1.STL
Documentation/3D Models/post_detailed_design_parts/power_mount.STL
Documentation/3D Models/post_detailed_design_parts/spacers.STL
Documentation/3D Models/post_detailed_design_parts/trolly2.STL
Documentation/3D Models/post_detailed_design_parts/trolly2mod.STL
Documentation/3D Models/pre_detailed_design_parts/CableChainEnds.stl
Documentation/3D Models/pre_detailed_design_parts/Electronic_Support_A.stl
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

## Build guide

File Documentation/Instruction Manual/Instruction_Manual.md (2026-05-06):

# Chess 2 Impress Instruction Manual 
This instruction manual will serve as a reference for starting up and maintaining our automated chess board. 

## Quick Startup Guide
1. Check and make sure that all cables on the Raspberry Pi/UPS are plugged in.
   This includes:
   - Booster wires
   - Uart Cable
   - All 4 USB Cables
   - Logic level converter and electromagnet cables (on Pi GPIO ports)
   - MicroHDMI cable for LCD screen

>Reference the troubleshooting section for a full diagram showing where everything should plug in.
  
2. Ensure that CoreXY is in correct position and electromagnet is all the way at home.
   - Electromagnet should be centered under the home square
   - CoreXY stand should line up with marks inside the base
  
>Reference the troubleshooting section for an image of the electromagnet home square.
3. Plug in LCD screen via HDMI and USB-C cables, then route screen through hole in acrylic.
4. Check that acrylic sheet is attached by all 4 corner screws.
5. Pull out USB coupler from board, press UPS power button one time, then reinsert USB coupler.
6. Check that UPS battery icons come on and that Raspberry Pi indicator light is green.
7. Plug microphone into USB coupler.
8. Screen should turn on and chess program should auto load. Follow prompts on LCD screen to play!

## Shutdown Guide
1. Say "Chess Resign" into the microphone and wait for the board to reset.
2. Once it is finished, say "Chess no" to tell the program to close.
3. Take all of the pieces off of the board, unplug LCD screen, unplug microphone, and put them away if chess board needs to be moved.
4. Take USB coupler out and press UPS power button 3 times to turn off.
5. Ensure that UPS charging light starts blinking red to show that it is charging.

## Diagrams and Troubleshooting
### Frequent Issues: 
__Software__
- __Issue__: The Pi is on but the screen will not turn on.
   - __Fix__: Make sure that both the HDMI and power cable to the LCD are plugged in well. If Pi stays on and LCD still does not turn on, try restarting the board.

- __Issue__: When I give the board a move, the motors do not move and the program goes to the next turn.
   - __Fix__: There is some issue with the arduino. Make sure that all of the GPIO pins are plugged in correctly and that both the UART and USB cables for the arduino are plugged in.

__Hardware__
- __Issue__: The belts on the CoreXY are making noise/slipping.
   - __Fix__: Turn off the board, manually move the CoreXY and see if it feels stuck/difficult to move the bar. Try to see if there is any part of the CoreXY that is rubbing against each other. Also measure both ends of the CoreXY and make sure that it is square. Otherwise, try retensioning the belts.

### Diagrams:

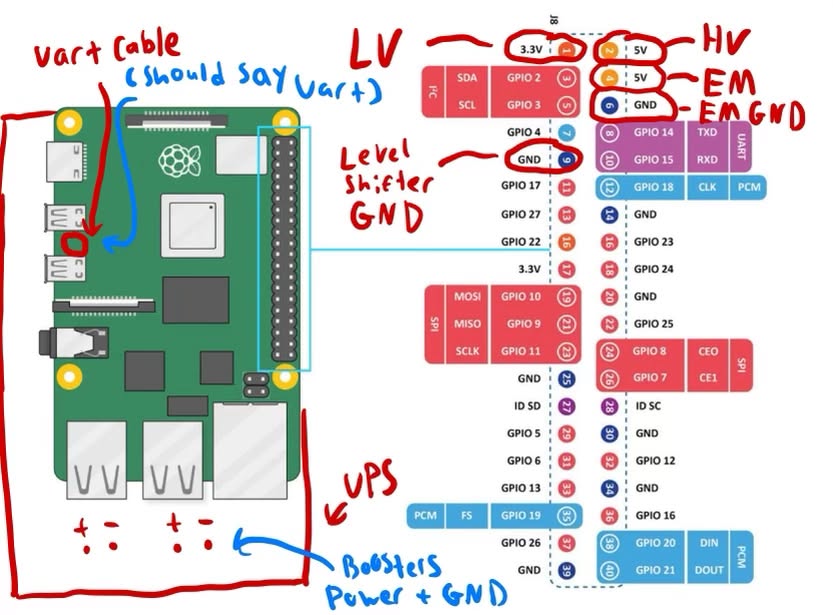
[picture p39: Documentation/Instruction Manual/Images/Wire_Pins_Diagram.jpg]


_Figure 1 - Raspberry Pi/UPS Wiring Diagram_

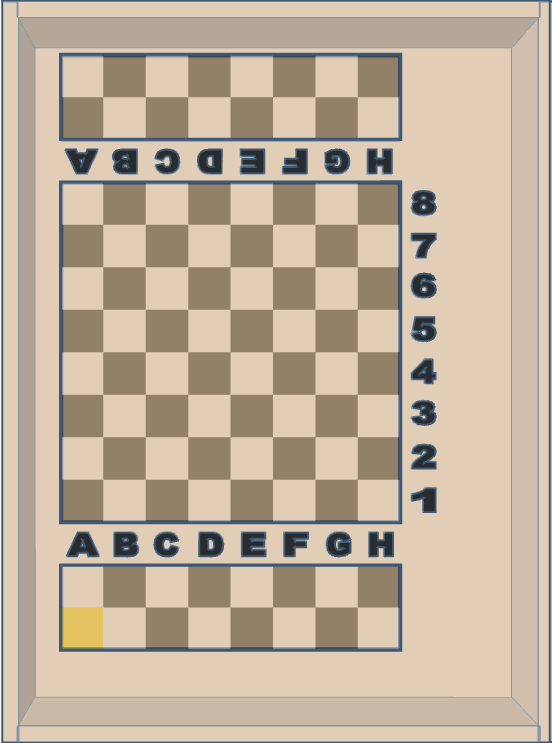
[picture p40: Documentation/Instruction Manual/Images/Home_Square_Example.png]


_Figure 2 - Electromagnet Home Square Example_

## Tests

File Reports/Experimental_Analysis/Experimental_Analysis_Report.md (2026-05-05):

# Experimental Analysis

**Project Title:** _Chess 2 Impress_

**Team Name:** _Team 2_

**Team Members:** _Allison Givens, Noah Beaty, Jack Tolleson, Lewis Bates, Nathan MacPherson_

**Course:** _ECE 4971_

**Instructor:** _Christopher Johnson_

**Submission Date:** _4-22-2026_

**Repository Link:** _https://github.com/TnTech-ECE/F25_Team2_AutomatedChessBoard_

---

## Table of Contents

1. [Introduction](#1-introduction)
2. [Critical Success Criteria](#2-critical-success-criteria)
3. [Experiment 1: Move Completion Time](#3-experiment-1-move-completion-time)
4. [Experiment 2: Boot Noise](#4-experiment-2-boot-noise)
5. [Experiment 3: Edge Boundary and Clamp Verification](#5-experiment-3-edge-boundary-and-clamp-verification)
6. [Experiment 4: Electromagnet Switching Latency](#6-experiment-4-electromagnet-switching-latency)
7. [Experiment 5: Flyback Diode Inductive Spike](#7-experiment-5-flyback-diode-inductive-spike)
8. [Experiment 6: Command Latency](#8-experiment-6-command-latency)
9. [Experiment 7: Voice Recognition Accuracy](#9-experiment-7-voice-recognition-accuracy)
10. [Experiment 8: Processing Latency / Display Responsiveness](#10-experiment-8-processing-latency--display-responsiveness)
11. [Experiment 9: Move Validation Correctness](#11-experiment-9-move-validation-correctness)
12. [Experiment 10: UART Communication Reliability](#12-experiment-10-uart-communication-reliability)
13. [Experiment 11: Thermal Safety](#13-experiment-11-thermal-safety)
14. [Experiment 12: Mechanical and Electrical Safety Compliance](#14-experiment-12-mechanical-and-electrical-safety-compliance)
15. [Experiment 13: UPS Switching Latency and Power-Loss Recovery](#15-experiment-13-ups-switching-latency-and-power-loss-recovery)
16. [Experiment 14: Board Weight](#16-experiment-14-board-weight)
17. [Experiment 15: Portability](#17-experiment-15-portability)
18. [Experiment 16: Sleep-Mode Power Draw](#18-experiment-16-sleep-mode-power-draw)
19. [Experiment 17: Battery Runtime](#19-experiment-17-battery-runtime)
20. [Experiment 18: Voltage Regulation, Ripple, and Electrical Safety](#20-experiment-18-voltage-regulation-ripple-and-electrical-safety)
21. [Experiment 19: Power Consumption and Budget Verification](#21-experiment-19-power-consumption-and-budget-verification)
22. [Summary of Findings](#22-summary-of-findings)
23. [Component Inventory](#23-component-inventory)
24. [Statement of Contributions](#24-statement-of-contributions)
25. [Appendix A: References](#25-appendix-a-references)

---

## 1. Introduction

### 1.1 Project Overview
The "_Chess 2 Impress_" automated chessboard is a low-cost, accessible, voice-controlled chess platform, combining traditional play with automated piece movement and AI opponent integration. The system captures spoken commands via a USB microphone, processes them using the Vosk speech recognition engine (on a Raspberry Pi), validates moves using python-chess (with Stockfish as the AI opponent in single-player mode), and executes physical moves through a CoreXY gantry (driven by an Arduino Nano and TMC2209 stepper drivers). An under-board electromagnet repositions the magnetic chess pieces without disturbing neighboring pieces. The project is aimed at chess enthusiasts, players with limited mobility or visual impairments, and hobbyists who want an automated chess experience at a fraction of commercial prices.

### 1.2 Purpose of This Report
This report documents the experimental evaluation of the _Chess 2 Impress_ system against the critical specifications and success criteria (established in the conceptual and detailed design documents). Each experiment is designed to quantitatively verify that a specific subsystem or integrated behavior meets its required performance, safety, or reliability target.

### 1.3 Scope
This report covers experiments evaluating the following aspects of the system:
- **Motion subsystem:** move completion time, edge boundary/clamp safety, positional accuracy
- **Electromagnet subsystem:** switching latency, inductive spike clamping, capture reliability
- **Communication subsystem:** UART command latency, communication reliability, boot-noise rejection
- **Voice/processing subsystem:** recognition accuracy, end-to-end processing latency, move validation correctness
- **Power and safety:** thermal limits, voltage rails, EMI practices, mechanical/electrical compliance, fault behavior

---

## 2. Critical Success Criteria

Below are the critical requirements and success criteria identified by the team and approved by the advisor. These are drawn directly from the conceptual design specifications.

| # | Criterion | Target / Specification | Source (Customer Need / Design Requirement) | Associated Experiment |
|---|---|---|---|---|
| 1 | Piece movement completion time | ≤ 5 seconds per move | Gameplay pacing / customer experience | Experiment 1 |
| 2 | Boot-noise rejection | No motion before `0x11` handshake | Safety / system integrity | Experiment 2 |
| 3 | CoreXY travel bounds | X ∈ [0.5, 7.5], Y ∈ [0.5, 13.5] squares | Mechanical safety / rail protection | Experiment 3 |
| 4 | Electromagnet switching latency | ≤ 10 ms on and off | Reliable piece pickup/release | Experiment 4 |
| 5 | Flyback diode clamping | Peak Vds ≤ 55 V (IRLZ44N max) | MOSFET protection / system longevity | Experiment 5 |
| 6 | Command latency (Arduino processing time) | ≤ 50 ms | Responsiveness / user experience | Experiment 6 |
| 7 | Voice recognition accuracy | ≥ 80% | Accessibility / usability | Experiment 7 |
| 8 | End-to-end processing latency (Pi) | ≤ 5 seconds from end of speech to display | Gameplay pacing | Experiment 8 |
| 9 | Move validation correctness | 100% correct legal/illegal classification | Game integrity | Experiment 9 |
| 10 | UART communication reliability | Error-free command transfer during full game | System reliability | Experiment 10 |
| 11 | Thermal safety | All surfaces ≤ 40 °C (104 °F) | UL 94 / CPSC 16 CFR 1505.7 | Experiment 11 |
| 12 | Mechanical & electrical safety compliance | Pass standardized inspection checklist (no Critical failures) | NEC / OSHA / ANSI Z535.4 [8][9][10] | Experiment 12 |
| 13 | UPS switchover and power-loss recovery | Clean UPS switchover with no Pi brownout or reboot; safe halt and clean recovery from wall-power loss | Conceptual design / reliability | Experiment 13 |
| 14 | Board weight | < 30 lb total | Customer accessibility / portability (Conceptual Design §Specifications item 4) | Experiment 14 |
| 15 | Portability | One person can lift, carry 10 yards, return 10 yards, and set down without excessive strain or damage | Customer accessibility / portability | Experiment 15 |
| 16 | Sleep-mode power draw | Sleep-mode input power draw consistent with Power_Budget.md (low-single-digit W) | Power_Budget.md | Experiment 16 |
| 17 | Battery runtime | ≥ 2 hr continuous gameplay from fully charged 4×18650 pack | Power_Budget.md / Conceptual Design | Experiment 17 |
| 18 | Voltage safety and low-noise design | All rails < 50 V DC; ripple < 5% p-p; low-noise design (no interference on nearby consumer electronics) | UL low-voltage threshold [2]; FCC Part 15 Subpart B [1] | Experiment 18 |
| 19 | Power consumption and budget verification | Measured rail and input power within 10% of Power_Budget.md; calculated UPS and MT3608 efficiencies within expected range | Power_Budget.md / Power_Tree.md | Experiment 19 |
| X1 | Collision-free movement rate | ≥ 95% of moves collision-free | Conceptual design (Arduino spec) | Collision Rate (un-testable) |
| X2 | Positional accuracy | ±0.5 mm across board | Precise piece placement | Positional Accuracy (un-testable) |

**Advisor Approval:**
- Approved by: _Dr. Van Neste_
- Date: _04-22-2026_

---

## 3. Experiment 1: Move Completion Time

### 3.1 Purpose and Justification
Verify that any single piece movement completes within 5 seconds of arriving at the source square, as specified in both the conceptual design and detailed design. This directly impacts gameplay pacing and user experience (slow moves frustrate players and reduce the perceived quality of the automated board).

### 3.2 Hypothesis / Expected Results
All move categories (short straight, long diagonal, knight, discard, and capture sequences) will complete under the 5-second spec, with long diagonal and full-field traverses taking the most time (expected ~3-4 s). Short straight moves are expected to complete in under 1 s.

### 3.3 Procedure

**Environmental Conditions:**
- Standard indoor lab conditions, room temperature, normal lighting.

**Preparation Steps:**
1. Connect the Arduino Nano to the Pi via UART.
2. Verify belt tension on both CoreXY axes.
3. Home the system to (0.5, 0.5) and place the board in a known state.

**Procedure Steps:**
1. Execute the following move categories, one at a time, recording completion time for each:
   - **Short straight:** a1 → a2 (1 square vertical)
   - **Medium straight:** a1 → a4 (3 squares vertical)
   - **Long straight:** a1 → a8 (7 squares vertical, full playing-field traverse)
   - **Diagonal:** a1 → c3 (2 squares diagonal)
   - **Long diagonal:** a1 → h8 (7 squares diagonal)
   - **Knight:** a1 → b3 (standard L-move)
   - **Discard (straight):** a1 → a11 (playing field to discard row)
   - **Long discard (L-shaped):** h8 → a11 (L-shaped path to discard row)
   - **Capture sequence:** a1 → a11 (piece to discard), then a8 → a1 (attacker to destination)
2. For each move, record time from when the piece is grabbed at its starting position to when it is dropped off at its ending position.
3. Re-home between categories to eliminate cumulative positional drift.

### 3.4 Data Collection Plan

| Variable | Units | Measurement Method | Frequency | Recording Format |
|---|---|---|---|---|
| Elapsed time | seconds | Phone Timer (start on grab, stop on release) | Per trial | Spreadsheet |
| Move category | — | Manual log | Per trial | Spreadsheet |
| Source / destination | square | Manual log | Per trial | Spreadsheet |
| Exceeds 5 s | Y/N | Derived from time | Per trial | Spreadsheet |

### 3.5 Trials
- **Number of trials:** N = 10 per category.
- **Justification:** The variety of categories ensures full coverage of the motion system; 10 trials per category provides meaningful mean and max values.

### 3.6 Potential Biases and Mitigation

| Potential Bias / Source of Error | Mitigation Strategy |
|---|---|
| Mechanical friction varies with board position | Test moves across different regions of the board |
| Belt tension changes over time | Check belt tension before the test session |
| Human timer reaction time | Use a single operator; average across many trials |

### 3.7 Actual Results

**Raw Data:**

| Trial | Move Category | Source → Dest | Elapsed Time (s) | Notes |
|---|---|---|---|---|
| 1 | Short straight | a1 → a2 | 5.58 | Exceeds 5 s spec |
| 2 | Medium straight | a1 → a4 | 8.13 | Exceeds 5 s spec |
| 3 | Long straight | a1 → a8 | 12.86 | Exceeds 5 s spec |
| 4 | Diagonal | a1 → c3 | 9.30 | Exceeds 5 s spec |
| 5 | Long diagonal | a1 → h8 | 22.04 | Exceeds 5 s spec |
| 6 | Knight | a1 → b3 | 11.21 | Exceeds 5 s spec |
| 7 | Discard (straight) | a1 → a11 | 7.94 | Exceeds 5 s spec |
| 8 | Long discard (L-shaped) | h8 → a11 | 30.00 | Exceeds 5 s spec (worst case) |
| 9 | Capture seq 1 (piece → discard) | a1 → a11 | 8.34 | Exceeds 5 s spec |
| 10 | Capture seq 2 (attacker → dest) | a8 → a1 | 12.63 | Exceeds 5 s spec |

**Summary Statistics:**
- Overall mean: 12.80 s
- Min: 5.58 s (shortest move, still exceeds spec)
- Max: 30.00 s (long L-shaped discard)
- Number of trials exceeding 5 s: **10 / 10**

### 3.8 Interpretation and Conclusions
The system failed to meet the 5-second spec on every single trial, including the shortest possible move. The overall mean of 12.8 s is more than double the target, and worst-case moves approach 30 s. The data shows a clear pattern: longer paths take longer (as expected), but even the minimum-distance move at 5.58 s falls outside the spec. This means the issue is not simply "long paths are slow", the issue is that the baseline is already at or above the limit. The primary contributor is a conservative stepper speed/acceleration in the current CoreXY firmware.

### 3.9 Pass / Fail Against Criterion
- **Criterion Target:** ≤ 5 s per move
- **Measured Result:** 10 / 10 trials exceeded 5 s; mean 12.80 s, max 30.00 s
- **Outcome:** Fail

### 3.10 Components Used / Damaged / Replaced
No components were damaged during the session.
- _Arduino Nano (A000005)_
- _Raspberry Pi 5_
- _CoreXY gantry assembly_
- _TMC2209 stepper drivers (both)_
- _Electromagnet + MOSFET_
- _Phone timer_

---

## 4. Experiment 2: Boot Noise

### 4.1 Purpose and Justification
Verify that the Control Unit (Arduino) ignores all UART traffic during Raspberry Pi boot until the `0x11` handshake byte is received. This behavior is implemented in the `piReady` flag. Without this protection, random characters sent by the Pi during boot could be misinterpreted as move commands and cause unintended motion (which is a safety hazard for both the mechanism and anyone near the board).

### 4.2 Hypothesis / Expected Results
The carriage will remain stationary throughout the about-45-second Pi boot. After `0x11` is received, the next valid command will execute normally. We expect 3/3 passes.

### 4.3 Procedure

**Environmental Conditions:**
- Standard indoor lab conditions.

**Preparation Steps:**
1. Power off the entire system.
2. Mark the carriage position with a piece of tape on the rail.

**Procedure Steps:**
1. Full power-cycle the system with the Pi connected.
2. Observe the carriage continuously during the about-45-second Pi boot. Verify no movement occurs.
3. After the chess software sends `0x11`, send a valid command and verify it executes correctly.
4. Power off and repeat for 3 total cold boots.

### 4.4 Data Collection Plan

| Variable | Units | Measurement Method | Frequency | Recording Format |
|---|---|---|---|---|
| Boot-time movement | Y/N | Visual observation | Per trial | Pass/fail table |
| `0x11` received | Y/N | Correct Execution | Per trial | Pass/fail table |
| Post-handshake command executed | Y/N | Visual | Per trial | Pass/fail table |

### 4.5 Trials
- **Number of trials:** N = 3 cold boots.
- **Justification:** Boot noise varies slightly between boots; 3 trials confirms repeatability of the handshake gate.

### 4.6 Potential Biases and Mitigation

| Potential Bias / Source of Error | Mitigation Strategy |
|---|---|
| Boot noise varies between boots | Test across 3 separate cold boots |

### 4.7 Actual Results

| Trial | Boot Movement (Y/N) | Start Command Received (Y/N) | Valid Command Executed (Y/N) | Pass/Fail |
|---|---|---|---|---|
| 1 | No | Yes | Yes | Pass |
| 2 | No | Yes | Yes | Pass |
| 3 | No | Yes | Yes | Pass |

**Summary Statistics:** Pass rate: 3 / 3 (100%)

### 4.8 Interpretation and Conclusions
The `piReady` flag successfully gated all UART input during boot across all three cold-boot trials. The carriage remained stationary during each about-45-second Pi boot, the handshake byte `0x11` was correctly received in every trial, and the first valid post-handshake command executed correctly every time. This confirms that boot-time noise on the UART line cannot trigger spurious motion.

### 4.9 Pass / Fail Against Criterion
- **Criterion Target:** No motion during boot; handshake required before commands execute
- **Measured Result:** 3 / 3 pass
- **Outcome:** Pass

### 4.10 Components Used / Damaged / Replaced
No components were damaged.
- _Arduino Nano (A000005)_
- _Raspberry Pi 5_
- _CoreXY gantry assembly_

---

## 5. Experiment 3: Edge Boundary and Clamp Verification

### 5.1 Purpose and Justification
Verify that the software clamping logic prevents the CoreXY head from moving beyond the center of any edge square (X ∈ [0.5, 7.5], Y ∈ [0.5, 13.5] in square units), and that the edge-travel algorithm correctly avoids the outermost board edges. This is a safety-critical requirement, as exceeding travel limits could damage the CoreXY mechanism or dislodge the carriage from the rails.

### 5.2 Hypothesis / Expected Results
Clamping logic will hold the carriage within the specified X and Y bounds for all four tested boundary conditions. Expected: 4/4 passes.

### 5.3 Procedure

**Environmental Conditions:**
- Standard indoor lab conditions.

**Preparation Steps:**
1. Home the system to (0.5, 0.5).
2. Visually confirm the rail limits on each of the four sides.

**Procedure Steps:**
1. Execute the following edge/boundary moves:
   - **Column a vertical:** a1 → a8 (X must not reach 0.0)
   - **Column h vertical:** h1 → h8 (X must not reach 8.0)
   - **Discard from column a:** a1 → a11 (Y must not go below 0.5)
   - **Discard from column h:** h8 → h10 (Y must not go above 13.5)
2. Visually confirm the carriage never reaches or crosses the outermost rail.
3. Record pass/fail. If a violation is observed, record approximate position and axis.
4. Re-home between each trial to prevent cumulative error.

### 5.4 Data Collection Plan

| Variable | Units | Measurement Method | Frequency | Recording Format |
|---|---|---|---|---|
| Boundary tested | X min / X max / Y min / Y max | Test case assignment | Per trial | Table |
| Carriage stayed within bounds | Y/N | Visual observation | Per trial | Table |
| Violation position (if any) | square units | Visual estimate | As needed | Table |

### 5.5 Trials
- **Number of trials:** N = 4 (one per boundary condition).
- **Justification:** Covers all four possible rail-collision concerns.

### 5.6 Potential Biases and Mitigation

| Potential Bias / Source of Error | Mitigation Strategy |
|---|---|
| Cumulative positional error from prior moves | Re-home between trials |

### 5.7 Actual Results

| Test Move | Source | Destination | Boundary Tested | Stayed Within Bounds (Y/N) |
|---|---|---|---|---|
| a1 → a8 | a1 | a8 | X left (X min) | Y |
| h1 → h8 | h1 | h8 | X right (X max) | Y |
| a1 → a11 | a1 | a11 | Y bottom (Y min) | Y |
| h8 → h10 | h8 | h10 | Y top (Y max) | Y |

**Summary Statistics:** Pass rate: 4 / 4 (100%)

### 5.8 Interpretation and Conclusions
The software clamping logic successfully constrained the carriage to within the specified X and Y bounds on all four boundary tests. The carriage never reached or crossed the outermost physical rail on any side during these trials. This confirms that the edge-travel algorithm and the clamping code in the CoreXY firmware work as designed, and that the mechanism is protected from rail collisions that could dislodge the carriage.

### 5.9 Pass / Fail Against Criterion
- **Criterion Target:** Carriage remains within X ∈ [0.5, 7.5], Y ∈ [0.5, 13.5] for all moves
- **Measured Result:** 4 / 4 pass
- **Outcome:** Pass

### 5.10 Components Used / Damaged / Replaced
No components were damaged.
- _Arduino Nano (A000005)_
- _CoreXY gantry assembly_

---

## 6. Experiment 4: Electromagnet Switching Latency

### 6.1 Purpose and Justification
Verify that the MOSFET-based electromagnet switching circuit activates within 10 ms, as specified in the detailed design. Quick pickup/release is essential, as a dropped piece mid-move ruins the game (from the customer's perspective).

### 6.2 Hypothesis / Expected Results
Turn-on and turn-off latencies will both be well under 10 ms.

### 6.3 Procedure

**Environmental Conditions:**
- Standard indoor lab conditions.

**Preparation Steps:**
1. Attach oscilloscope probes to the Arduino's MAGNET_PIN (D10) output and to the MOSFET drain.

**Procedure Steps:**
1. Command the Arduino to toggle the electromagnet on and off using `magnetOn()` and `magnetOff()` in a test loop with 2-second delays between toggles.
2. Measure the time from the rising edge of the gate signal to the point where drain current reaches 90% of steady state (turn-on latency).
3. Measure the time from the falling edge of the gate signal to the point where drain current drops below 10% (turn-off latency).
4. Repeat for 10 switching cycles.

### 6.4 Data Collection Plan

| Variable | Units | Measurement Method | Frequency | Recording Format |
|---|---|---|---|---|
| Turn-on latency | µs | Oscilloscope cursor | Per cycle | Spreadsheet |
| Turn-off latency | µs | Oscilloscope cursor | Per cycle | Spreadsheet |

### 6.5 Trials
- **Number of trials:** N = 10 switching cycles.
- **Justification:** Ten measurements provide reliable mean and max values to confirm the <10 ms spec.

### 6.6 Potential Biases and Mitigation

| Potential Bias / Source of Error | Mitigation Strategy |
|---|---|
| Oscilloscope bandwidth limits edge precision | Use a scope with ≥ 20 MHz bandwidth |

### 6.7 Actual Results

| Trial | Turn-On Latency (µs) | Turn-Off Latency (µs) |
|---|---|---|
| 1  | 3.0 | 3.0 |
| 2  | 2.7 | 2.8 |
| 3  | 3.0 | 2.9 |
| 4  | 2.8 | 2.9 |
| 5  | 2.6 | 2.7 |
| 6  | 3.0 | 3.0 |
| 7  | 2.7 | 2.6 |
| 8  | 2.8 | 2.8 |
| 9  | 2.9 | 3.0 |
| 10 | 2.8 | 2.7 |

**Summary Statistics:**
- Turn-on: Mean 2.83 µs, Max 3.0 µs
- Turn-off: Mean 2.84 µs, Max 3.0 µs
- Both values are about 3300× faster than the 10 ms spec.

**Visualizations:**

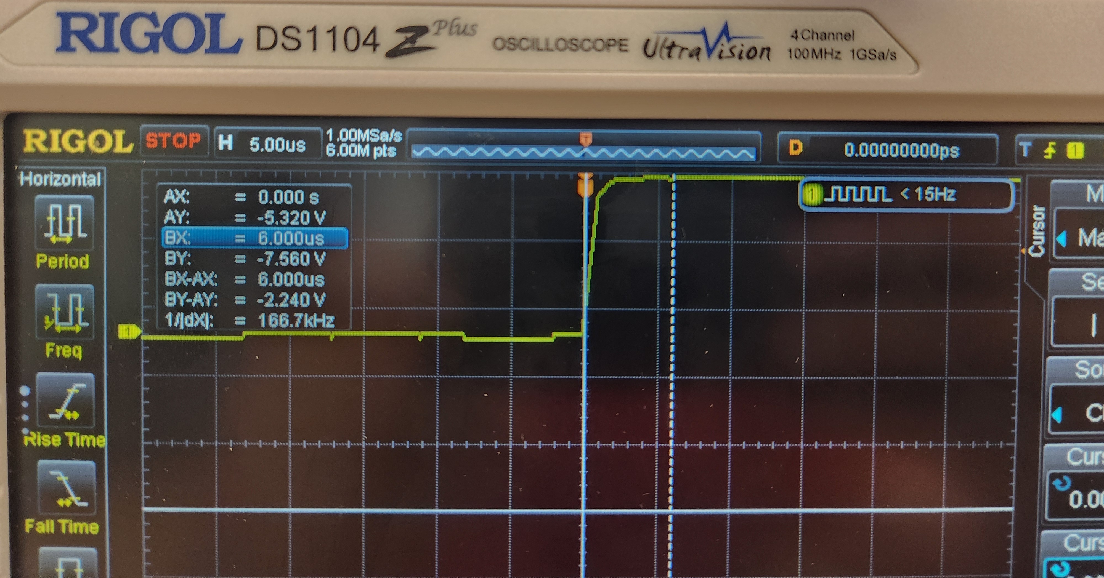
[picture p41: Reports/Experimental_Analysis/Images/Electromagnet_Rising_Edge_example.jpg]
Electromagnet turn-on rising edge on oscilloscope


_Figure 6.1 — Oscilloscope capture of the gate and drain waveforms during electromagnet turn-on (rising edge)._

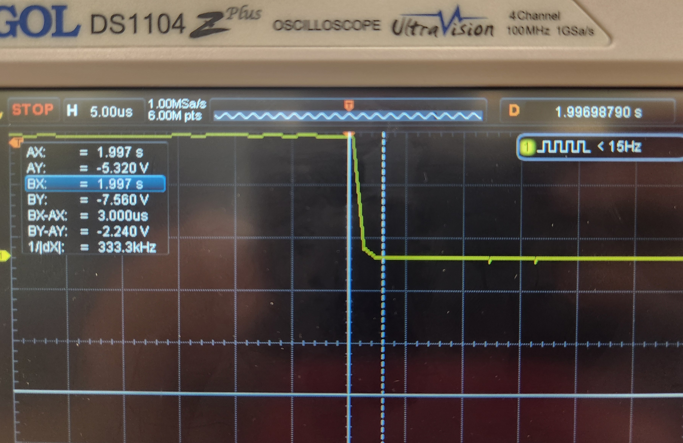
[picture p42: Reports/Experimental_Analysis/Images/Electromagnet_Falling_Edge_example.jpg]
Electromagnet turn-off falling edge on oscilloscope


_Figure 6.2 — Oscilloscope capture of the gate and drain waveforms during electromagnet turn-off (falling edge)._

### 6.8 Interpretation and Conclusions
Turn-on and turn-off latencies are both in the low-microsecond range, far below the 10 ms specification. The IRLZ44NPBF logic-level MOSFET responds almost immediately to the gate signal, and the measured variation between trials (2.6–3.0 µs) is small enough to be attributable to measurement noise and cursor placement on the oscilloscope. This result demonstrates that the electromagnet switching path introduces negligible delay into the overall move-completion budget.

### 6.9 Pass / Fail Against Criterion
- **Criterion Target:** ≤ 10 ms turn-on and turn-off
- **Measured Result:** Max 3.0 µs on both edges
- **Outcome:** Pass

### 6.10 Components Used / Damaged / Replaced
No components were damaged.
- _Arduino Nano (A000005)_
- _IRLZ44NPBF MOSFET_
- _Electromagnet coil_
- _Oscilloscope (≥ 20 MHz bandwidth)_

---

## 7. Experiment 5: Flyback Diode Inductive Spike

### 7.1 Purpose and Justification
Verify that the flyback diode clamps the inductive voltage spike on the MOSFET drain to within the IRLZ44NPBF's maximum Vds rating (55 V) when the electromagnet is switched off. An unclamped spike could destroy the MOSFET, causing permanent system failure.

### 7.2 Hypothesis / Expected Results
The clamped spike will peak well below 55 V (expected about 13–15 V, just above the 12 V rail) and remain essentially constant (regardless of energization duration).

### 7.3 Procedure

**Environmental Conditions:**
- Standard indoor lab conditions; ambient temperature recorded per trial.

**Preparation Steps:**
1. Connect the oscilloscope probe to the MOSFET drain pin with the shortest possible ground lead.
2. Set scope to trigger on falling edge of the gate signal; set vertical scale sufficient to capture spikes up to 60 V.

**Procedure Steps:**
1. Command the Arduino to energize the electromagnet for the specified on-duration, then switch off.
2. Capture the drain voltage waveform during the off-switching event.
3. Record the peak voltage spike magnitude and its duration.
4. Repeat for on-durations of 200 ms, 1 s, 2 s, and 5 s.

### 7.4 Data Collection Plan

| Variable | Units | Measurement Method | Frequency | Recording Format |
|---|---|---|---|---|
| On-duration | s | Test case parameter | Per trial | Table |
| Peak spike voltage | V | Oscilloscope cursor | Per trial | Table |
| Ambient temperature | °F | Thermometer | Per trial | Table |
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

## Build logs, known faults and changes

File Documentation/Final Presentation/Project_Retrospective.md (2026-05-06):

# Project Retrospective

## Lessons Learned

- **Order and test parts as early as possible.** Our first screen arrived faulty and took out needed GPIO voltage pins. Because we tested early, we were able to reorder before it became a bottleneck.
- **Flatness of the playing surface is a critical mechanical requirement.** Individually, the acrylic bow, the mid-span wooden support, and the uneven CoreXY frame supports looked like minor assembly issues, but together they made two of our planned tests impossible to run.
- **Account for wire AWG throughout the design process** to manage thermal and current-load concerns.
- **Build small-scale prototypes and assemble all CAD drawings together** to physically surface design flaws earlier.
- **Be generous with tolerances.** It is always easier to remove more material later than to recover from removing too much.

## Future Work

### Playing Surface and Structure
- Improve playing-surface flatness with a stiffer board or additional supports to ensure consistent electromagnet pickup.
- Add a glass top (in place of the acrylic) for greater rigidity.
- If a glass top is added, sand down or shorten the wooden midsection support to match.

### Electromagnet and Pieces
- Replace the electromagnet with a stronger, higher-voltage alternative so it can sit lower and pieces no longer need to rely on base magnets to be held.
- Swap the current electromagnet mount for a lower-height mount. If the electromagnet is upgraded to a stronger one, raise the mount instead and reintroduce the washers in each chess piece in place of the neodymium magnets currently at each piece's base.

### Motion System
- Increase motion speed by raising the available motor voltage, optimizing microstepping settings, and reducing frictional losses in the CoreXY path.
- Improve adhesion of the jumper wires (for the stepper motor boosters) to the UPS.

### Software and AI
- Add selectable difficulty levels for the AI.
- Add the ability to redo moves.
- Fix an Arduino bug in the capture routine: pieces are occasionally dragged through the middle of the squares in the top or bottom discard rows.

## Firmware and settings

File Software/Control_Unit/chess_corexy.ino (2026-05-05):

#include <AccelStepper.h>
#include <EEPROM.h>

// pin definitions
#define STEP_A    2
#define DIR_A     3
#define EN_A      4
#define DIAG_A    5

#define STEP_B    6
#define DIR_B     7
#define EN_B      8
#define DIAG_B    9

#define MAGNET_PIN 10

// motion constants
#define SQUARE_SIZE_MM     57.15f
#define STEPS_PER_MM       40.0f
#define STEPS_PER_SQUARE   (long)(SQUARE_SIZE_MM * STEPS_PER_MM)

// board extents (in chess squares)
#define BOARD_COLS         8
#define BOARD_ROWS         14
// valid head range (centers of edge squares are the limits)
#define X_MIN  0.5f
// 7.5
#define X_MAX  ((float)BOARD_COLS - 0.5f)
#define Y_MIN  0.5f
// 13.5
#define Y_MAX  ((float)BOARD_ROWS - 0.5f)

// EEPROM layout
#define EEPROM_MAGIC      0xAB
#define EEPROM_ADDR_MAGIC 0
// long (4 bytes)
#define EEPROM_ADDR_A     2
#define EEPROM_ADDR_B     6

// global variables
AccelStepper motorA(AccelStepper::DRIVER, STEP_A, DIR_A);
AccelStepper motorB(AccelStepper::DRIVER, STEP_B, DIR_B);

bool magnetState    = false;
bool faultOccurred  = false;
bool piReady = false;


// EEPROM help functions

void savePosition() {
  long a = motorA.currentPosition();
  long b = motorB.currentPosition();
  EEPROM.update(EEPROM_ADDR_MAGIC, EEPROM_MAGIC);
  EEPROM.put(EEPROM_ADDR_A, a);
  EEPROM.put(EEPROM_ADDR_B, b);
}

bool loadPosition() {
  if (EEPROM.read(EEPROM_ADDR_MAGIC) != EEPROM_MAGIC) return false;
  long a, b;
  EEPROM.get(EEPROM_ADDR_A, a);
  EEPROM.get(EEPROM_ADDR_B, b);
  motorA.setCurrentPosition(a);
  motorB.setCurrentPosition(b);
  return true;
}

void clearSavedPosition() {
  EEPROM.update(EEPROM_ADDR_MAGIC, 0x00);
}


// fault tolerance

bool checkFault() {
  if (digitalRead(DIAG_A) == HIGH || digitalRead(DIAG_B) == HIGH) {
    // disable drivers
    digitalWrite(EN_A, HIGH);
    digitalWrite(EN_B, HIGH);
    motorA.stop();
    motorB.stop();
    magnetOff();
    faultOccurred = true;
    // preserve where last stopped
    savePosition();
    return true;
  }
  return false;
}

void enableDrivers() {
  digitalWrite(EN_A, LOW);
  digitalWrite(EN_B, LOW);
  faultOccurred = false;
}


// magnet functions

void magnetOn() {
  digitalWrite(MAGNET_PIN, HIGH);
  magnetState = true;
}

void magnetOff() {
  digitalWrite(MAGNET_PIN, LOW);
  magnetState = false;
}


// CoreXY move (low level movement)

void moveToSteps(long a, long b) {
  if (faultOccurred) return;
  motorA.moveTo(a);
  motorB.moveTo(b);
  while (motorA.distanceToGo() != 0 || motorB.distanceToGo() != 0) {
    if (checkFault()) return;
    motorA.run();
    motorB.run();
  }
  savePosition();
}

// XY coordinate moves
// square-unit float variables to step positions

float clampX(float x) { return (x < X_MIN) ? X_MIN : (x > X_MAX) ? X_MAX : x; }
float clampY(float y) { return (y < Y_MIN) ? Y_MIN : (y > Y_MAX) ? Y_MAX : y; }

void moveToXY(float xSq, float ySq) {
  xSq = clampX(xSq);
  ySq = clampY(ySq);
  // round
  long xSteps = (long)(xSq * STEPS_PER_SQUARE + 0.5f);
  long ySteps = (long)(ySq * STEPS_PER_SQUARE + 0.5f);
  long a = xSteps + ySteps;
  long b = xSteps - ySteps;
  moveToSteps(a, b);
}

void currentXY(float &xSq, float &ySq) {
  long a = motorA.currentPosition();
  long b = motorB.currentPosition();
  xSq = (float)(a + b) / 2.0f / (float)STEPS_PER_SQUARE;
  ySq = (float)(a - b) / 2.0f / (float)STEPS_PER_SQUARE;
}

// coordinate mapping
// Pi row or column to square units
// Pi rows 1–8 (playing field)
// (Pi row 1 to physical row 4) TO (Pi row 8 to physical row 11)
// Pi row 9 (black pawn discard) = physical row 13
// Pi row 10 (black special discard) = physical row 14
// Pi row 11 (white special discard) = physical row 1
// Pi row 12 (white pawn discard) = physical row 2

float piRowToPhysY(int piRow) {
  int physRow;
  switch (piRow) {
    // white special discard
    case 11: physRow =  1; break;

    // white pawn discard
    case 12: physRow =  2; break;

    // playing field bottom
    case  1: physRow =  4; break;

    case  2: physRow =  5; break;
    case  3: physRow =  6; break;
    case  4: physRow =  7; break;
    case  5: physRow =  8; break;
    case  6: physRow =  9; break;
    case  7: physRow = 10; break;

    // playing field top
    case  8: physRow = 11; break;

    // black pawn discard
    case  9: physRow = 13; break;

    // black special discard
    case 10: physRow = 14; break;

    // fallback
    default: physRow =  1; break;
  }
  // center of current row
  return (float)physRow - 0.5f;
}

float colToPhysX(int col) {
  // col 0 = a, 7 = h
  return (float)col + 0.5f;
}


// piece movement engine
void chooseExitEdge(float cx, float cy, int dx, int dy, float &ex, float &ey) {
  int adx = abs(dx);
  int ady = abs(dy);

  if (adx == 0 && ady == 0) {
    ex = cx + 0.5f; ey = cy;
    return;
  }

  if (adx == 0) {
    if (cx + 0.5f >= (float)BOARD_COLS) {
      ex = cx - 0.5f;
    } else {
      ex = cx + 0.5f;
    }
    ey = cy;
  } else if (ady == 0) {
    ex = cx;
    if (cy + 0.5f >= (float)BOARD_ROWS) {
      ey = cy - 0.5f;
    } else {
      ey = cy + 0.5f;
    }
  } else {
    // diagonal or knight = move to corner of source square toward the destination
    ex = cx + ((dx > 0) ? 0.5f : -0.5f);
    ey = cy + ((dy > 0) ? 0.5f : -0.5f);
  }
}

void chooseEntryEdge(float cx, float cy, int dx, int dy, float &ex, float &ey) {
  int adx = abs(dx);
  int ady = abs(dy);

  if (adx == 0 && ady == 0) {
    ex = cx - 0.5f; ey = cy;
    return;
  }

  if (adx == 0) {
    if (cx + 0.5f >= (float)BOARD_COLS) {
      ex = cx - 0.5f;
    } else {
      ex = cx + 0.5f;
    }
    ey = cy;
  } else if (ady == 0) {
    ex = cx;
    if (cy + 0.5f >= (float)BOARD_ROWS) {
      ey = cy - 0.5f;
    } else {
      ey = cy + 0.5f;
    }
  } else {
    // diagonal or knight = entry point on horizontal edge "lane" at destination column's center X
    ex = cx;
    ey = cy + ((dy > 0) ? 0.5f : -0.5f);
  }
}

void straightEdgeTravel(float fromX, float fromY, float toX,   float toY) {
  moveToXY(toX, toY);
}

void diagonalStaircaseTravel(float startX, float startY,
                             int dx, int dy, int steps) {
  float x = startX;
  float y = startY;
  float stepY = (dy > 0) ? (float)steps : (float)(-steps);

  // travel full Y distance along vertical edge lane
  y += stepY;
  moveToXY(x, y);

  // travel full X distance along horizontal edge lane (entry edge X handles the final position)
}

void knightLTravel(float startX, float startY, int dx, int dy) {
  float x = startX;
  float y = startY;
  int adx = abs(dx);
  int ady = abs(dy);
  float stepX = (dx > 0) ? 1.0f : -1.0f;
  float stepY = (dy > 0) ? 1.0f : -1.0f;

  // start at exit edge (cx ± 0.5, cy) on vertical edge lane
  // travel longer leg along current edge lane, then shorter leg along horizontal edge lane (to entry edge)

  if (ady >= adx) {
    // long leg in Y (travel along vertical edge lane)
    for (int i = 0; i < ady; i++) {
      y += stepY;
      moveToXY(x, y);
    }
    // short leg in X (at (cx ± 0.5, destY) and need to reach entry edge at (destCx - 0.5, destY))
    // for dx=1 at cx+0.5 = destCx-0.5, already arrived
    // for dx=2, would need one more step (not valid knight move)
  } else {
    // long leg in X (first move to horizontal edge lane by going to (cx ± 0.5, cy ± 0.5))
    y += stepY * 0.5f;
    moveToXY(x, y);
    // travel along horizontal edge lane
    for (int i = 0; i < adx; i++) {
      x += stepX;
      moveToXY(x, y);
    }
    // short leg in Y (travel to entry edge)
    // at (destCx + 0.5, cy ± 0.5) and need to reach (destCx - 0.5, destCy) = travel along vertical edge lane (shift first)
    x -= stepX * 0.5f;
    moveToXY(x, y);
    for (int i = 0; i < ady - 1; i++) {
      y += stepY;
      moveToXY(x, y);
    }
    y += stepY * 0.5f;
    moveToXY(x, y);
  }
}


// full piece move
void movePiece(int srcCol, int srcPiRow, int dstCol, int dstPiRow) {

  // home signal: "src == dst"
  if (srcCol == dstCol && srcPiRow == dstPiRow) {
    float px = colToPhysX(srcCol);
    float py = piRowToPhysY(srcPiRow);
    magnetOff();
    moveToXY(px, py);
    return;
  }

  // convert to physical square centers
  // source center X
  float sx = colToPhysX(srcCol);
  // source center Y
  float sy = piRowToPhysY(srcPiRow);
  // destination center X
  float dx_f = colToPhysX(dstCol);
  // destination center Y
  float dy_f = piRowToPhysY(dstPiRow);

  // direction in square units
  int totalDx = (int)roundf(dx_f - sx);
  int totalDy = (int)roundf(dy_f - sy);

  int dirX = (totalDx > 0) ? 1 : (totalDx < 0) ? -1 : 0;
  int dirY = (totalDy > 0) ? 1 : (totalDy < 0) ? -1 : 0;

  // determine move type
  int adx = abs(totalDx);
  int ady = abs(totalDy);
  bool isStraight = (dirX == 0 || dirY == 0);
  bool isDiagonal = (adx == ady && adx > 0);
  bool isKnight   = ((adx == 1 && ady == 2) || (adx == 2 && ady == 1));

  // approach: (magnet OFF) move directly to edge midpoint of the source square
  // use exit edge since needs to passthrough center
  float exitX, exitY;
  chooseExitEdge(sx, sy, totalDx, totalDy, exitX, exitY);

  magnetOff();
  // direct path (magnet off)
  moveToXY(exitX, exitY);

  // move to source center
  moveToXY(sx, sy);

  // turn on magnet
  magnetOn();
  delay(200);

  // return to exit-edge midpoint (magnet on, single axis move)
  moveToXY(exitX, exitY);

  // travel to destination (magnet on, edge lanes only)

  float entryX, entryY;
  chooseEntryEdge(dx_f, dy_f, totalDx, totalDy, entryX, entryY);

  if (isStraight) {
    straightEdgeTravel(exitX, exitY, entryX, entryY);
  } else if (isDiagonal) {
    diagonalStaircaseTravel(exitX, exitY, dirX, dirY, adx);
    moveToXY(entryX, entryY);
  } else if (isKnight) {
    knightLTravel(exitX, exitY, totalDx, totalDy);
    // after L-travel, should be at entry edge of destination
    // move precisely to entry edge (in case of float drift)
    moveToXY(entryX, entryY);
  } else {
    // general case = fall back to L-shaped path
    knightLTravel(exitX, exitY, totalDx, totalDy);
    moveToXY(entryX, entryY);
  }

  // enter destination center
  moveToXY(dx_f, dy_f);

  // release magnet
  magnetOff();
  delay(200);
}


// UART command parser
// binary format is 2 bytes per comman:d
// byte 1 (source): high nibble = col (a=1...h=8), low nibble = row (1...12)
// byte 2 (dest):   same as above

// special: "src==dst" is home signal, so navigate to position (without magnet on)
// startup handshake: Pi sends 0x11 after mic ready, Arduino waits before accepting move commands
// response: 0x01 = ACK (move complete), 0x00 = NACK (parse error or fault)

void sendAck()  { Serial.write((uint8_t)0x01); }
void sendNack() { Serial.write((uint8_t)0x00); }

// main
void setup() {
  Serial.begin(115200);

  pinMode(EN_A, OUTPUT);
  pinMode(EN_B, OUTPUT);
  pinMode(MAGNET_PIN, OUTPUT);
  pinMode(DIAG_A, INPUT_PULLUP);
  pinMode(DIAG_B, INPUT_PULLUP);

  magnetOff();
  enableDrivers();

  motorA.setMaxSpeed(4000);
  motorA.setAcceleration(1500);
  motorB.setMaxSpeed(4000);
  motorB.setAcceleration(1500);

  // assume head is at physical home on startup
  clearSavedPosition();

  // home to (0,0)
  //motorA.setCurrentPosition(0);
  //motorB.setCurrentPosition(0);

  // home to (0.5,0.5)
  long xSteps = (long)(0.5f * STEPS_PER_SQUARE + 0.5f);
  long ySteps = (long)(0.5f * STEPS_PER_SQUARE + 0.5f);
  motorA.setCurrentPosition(xSteps + ySteps);
  motorB.setCurrentPosition(xSteps - ySteps);

  // flush garbage bytes from startup
  delay(500);
  while (Serial.available()) Serial.read();
}

void loop() {
  if (!piReady) {
    // wait for Pi to send 0x11 (as "ready" signal)
    while (Serial.available()) {
      if (Serial.read() == 0x11) {
        piReady = true;
        break;
      }
    }
    return;
  }



  if (Serial.available() >= 2) {
    uint8_t srcByte = Serial.read();
    uint8_t dstByte = Serial.read();

    int srcCol = ((srcByte >> 4) & 0x0F) - 1;
    int srcRow = srcByte & 0x0F;
    int dstCol = ((dstByte >> 4) & 0x0F) - 1;
    int dstRow = dstByte & 0x0F;

    if (srcCol < 0 || srcCol > 7 ||
        dstCol < 0 || dstCol > 7 ||
        srcRow < 1 || srcRow > 12 ||
        dstRow < 1 || dstRow > 12) {
      while (Serial.available()) Serial.read();
      sendNack();
      return;
    }

    if (faultOccurred) {
      enableDrivers();
    }

    movePiece(srcCol, srcRow, dstCol, dstRow);

    if (faultOccurred) {
      sendNack();
    } else {
      clearSavedPosition();
      sendAck();
    }
  }




  //if (faultOccurred) { while (1); }

  //Serial.println("Test 1: Diagonal a1 -> c3");
  //movePiece(0, 1, 2, 3);
  //delay(3000);
  
  
  /*
  Serial.println("Test 2: Knight a1 -> b3");
  movePiece(0, 1, 1, 3);
  delay(3000);
  */

  
  /*
  Serial.println("Test 3: Straight a1 -> a6");
  movePiece(0, 1, 0, 6);
  delay(3000);
  */

  /*
  Serial.println("Test 4: a11 -> c1 (L-shaped)");
  movePiece(0, 11, 2, 1);
  delay(3000);
  */
  
  //Serial.println("test done, halting");
  //while (1);
  
}

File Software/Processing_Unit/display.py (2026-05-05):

"""
display.py — Pygame display for Voice Chess (800 × 480)

Usage in main script:
    from display import Display
    disp = Display()
    disp.set_status("White to move")
    disp.log_move(1, "e2e4", "e7e5")
    disp.set_message("Listening...", kind="info")
    disp.update_board(board)          # pass a chess.Board object
    disp.log_binary("e2e4", "0101 0010", "0101 0100")
    # On exit:
    disp.quit()
"""

import threading
import queue
import chess
import sys

try:
    import pygame
except ImportError:
    print("pygame not found — run: pip install pygame", file=sys.stderr)
    raise

# ── Layout constants (800 × 480) ──────────────────────────────────────────────
W, H          = 800, 480
BOARD_PX      = 368          # board square width/height (fits 8×46 squares)
SQ            = BOARD_PX // 8
BOARD_X       = 8            # left margin for board
BOARD_Y       = 8
RIGHT_X       = BOARD_X + BOARD_PX + 12   # x-start of right panel
RIGHT_W       = W - RIGHT_X - 8           # width of right panel

STATUS_H      = 40
HISTORY_Y     = BOARD_Y + STATUS_H + 6
HISTORY_H     = 160
MSG_Y         = HISTORY_Y + HISTORY_H + 6
MSG_H         = H - MSG_Y - 8
MSG_LINE_H    = 20
MSG_MAX_LINES = (MSG_H - 32) // MSG_LINE_H

# Captured pieces panel — sits below the board
CAP_Y         = BOARD_Y + BOARD_PX + 18   # below board + coord labels
CAP_H         = H - CAP_Y - 8             # ~78px remaining
CAP_W         = BOARD_PX                  # same width as the board

# Standard piece point values
PIECE_POINTS = {
    chess.PAWN:   1,
    chess.KNIGHT: 3,
    chess.BISHOP: 3,
    chess.ROOK:   5,
    chess.QUEEN:  9,
    chess.KING:   0,
}

# ── Palette ───────────────────────────────────────────────────────────────────
BG            = (18,  18,  20)
PANEL         = (30,  30,  34)
BORDER        = (60,  60,  66)
TEXT_PRI      = (220, 218, 210)
TEXT_SEC      = (130, 128, 120)
TEXT_MONO     = (170, 230, 170)
SQ_LIGHT      = (240, 217, 181)
SQ_DARK       = (181, 136,  99)
HIGHLIGHT     = (255, 215,   0)   # last-move highlight
WHITE_PIECE   = (245, 245, 240)
BLACK_PIECE   = ( 30,  30,  30)
PIECE_OUTLINE = (100, 100, 100)

MSG_COLORS = {
    "info":    ((40,  80, 140), (120, 180, 255)),
    "success": ((30,  90,  50), (100, 220, 130)),
    "error":   ((120, 30,  30), (255, 110, 110)),
    "warn":    ((110, 80,   0), (240, 190,  60)),
    "neutral": ((50,  50,  55), TEXT_SEC),
}

# Unicode piece glyphs — always use the solid (filled) black variant index 1
# for rendering. Color of the piece is conveyed by the draw color, not the glyph shape.
# White outline glyphs (♙♖etc) render hollow in most fonts; solid glyphs (♟♜etc)
# filled with WHITE_PIECE color look fully white on the board.
GLYPHS = {
    chess.PAWN:   ("♟", "♟"),
    chess.ROOK:   ("♜", "♜"),
    chess.KNIGHT: ("♞", "♞"),
    chess.BISHOP: ("♝", "♝"),
    chess.QUEEN:  ("♛", "♛"),
    chess.KING:   ("♚", "♚"),
}


class Display:
    """
    Thread-safe Pygame display.  All drawing happens on the main thread via an
    internal command queue; call public methods from any thread.
    """

    def __init__(self):
        self._q: queue.Queue = queue.Queue()
        self._state = {
            "board":      chess.Board(),
            "last_move":  None,
            "status":     "Ready",
            "status_sub": "",
            "history":    [],          # list of (move_no, white_uci, black_uci|"")
            "binary":     ("", "", ""),# (uci, src_bits, dst_bits)
            "messages":   [("Microphone active. Listening…", "info")],  # rolling log
        }
        self._thread = threading.Thread(target=self._run, daemon=True)
        self._thread.start()
        # Wait for Pygame to initialise before returning
        self._ready = threading.Event()
        self._ready.wait()

    # ── Public API (thread-safe) ──────────────────────────────────────────────

    def update_board(self, board: chess.Board, last_move=None):
        """Push a new board state.  last_move is a chess.Move or None."""
        import copy
        self._q.put(("board", copy.copy(board), last_move))

    def set_status(self, text: str, sub: str = ""):
        """Top-right banner: e.g. 'White to move', sub='Stockfish Elo 1350'."""
        self._q.put(("status", text, sub))

    def log_move(self, move_no: int, white_uci: str, black_uci: str = ""):
        """Append a move pair to the history log."""
        self._q.put(("move", move_no, white_uci, black_uci))

    def log_binary(self, uci: str, src_bits: str, dst_bits: str):
        """Display the binary encoding of the last move."""
        self._q.put(("binary", uci, src_bits, dst_bits))

    def clear_log(self):
        """Clear the move history, binary display, and message log."""
        self._q.put(("clear_log",))

    def set_message(self, text: str, kind: str = "info"):
        """Append to the message log.  kind: 'info' | 'success' | 'error' | 'warn' | 'neutral'"""
        self._q.put(("message", text, kind))

    def quit(self):
        self._q.put(("quit",))
        self._thread.join(timeout=3)

    # ── Internal render loop (main thread) ───────────────────────────────────

    def _run(self):
        pygame.init()
        # Try true fullscreen first; fall back to a borderless window
        try:
            self._screen = pygame.display.set_mode(
                (W, H), pygame.FULLSCREEN | pygame.NOFRAME
            )
        except Exception:
            self._screen = pygame.display.set_mode((W, H))

        pygame.display.set_caption("Voice Chess")
        pygame.mouse.set_visible(False)

        # Fonts — fall back gracefully if a system font is missing
        def _font(size, bold=False, mono=False):
            families = (
                ["DejaVu Sans Mono", "Courier New", "monospace"] if mono
                else ["DejaVu Sans", "Liberation Sans", "Arial", "sans-serif"]
            )
            for fam in families:
                try:
                    return pygame.font.SysFont(fam, size, bold=bold)
                except Exception:
                    pass
            return pygame.font.Font(None, size)

        self._fnt_piece   = _font(36, mono=True)   # chess glyphs
        self._fnt_label   = _font(14)              # board coordinates
        self._fnt_body    = _font(17)
        self._fnt_body_b  = _font(17, bold=True)
        self._fnt_mono    = _font(15, mono=True)
        self._fnt_head    = _font(19, bold=True)
        self._fnt_msg     = _font(18)

        self._ready.set()
        clock = pygame.time.Clock()

        while True:
            # Drain the command queue
            try:
                while True:
                    cmd = self._q.get_nowait()
                    self._apply(cmd)
                    if cmd[0] == "quit":
                        pygame.quit()
                        return
            except queue.Empty:
                pass
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

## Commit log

2025-10-10 Added stepper driver boards
2025-10-10 Added all stepper motors
2025-10-12 Added first of minimum 3 magnetic solutions
2025-10-12 second magnet option
2025-10-12 finished flow chart
    Added sections for Processing Unit, Control Unit, Core XY Unit, Peripherals Unit, and Power Unit in the hardware block diagram. Expanded the operational flow chart description to include user interac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
2025-10-13 adding photos
    Updated the operational flow chart with a block diagram image.
2025-10-14 Power systems complete
2025-10-27 Added Power subsystem images
2025-11-13 Rename Capstone I - Control Unit Flowchart.png to Control-Unit-Flowchart.png
2025-11-13 Added flowchart
2025-11-14 changing electromagnet voltage
2025-11-17 Added heatsink info
2025-11-17 partial bom
2025-11-17 adding parts
    [2018_CableCarriers_1.stl, 2020_aluminum_extrusion.SLDPRT, 2020_aluminum_extrusion_face.stl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]
2025-11-17 added frame to bom
2025-11-17 changing files from sldprt to stl
    [2020_aluminum_extrusion.SLDPRT, 2020_aluminum_extrusion.STL, angle_bracket.SLDPRT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]
2025-11-17 adding parts to 3D models
    [2018_CableCarriers_1.stl, 2020_aluminum_extrusion.STL, 2020_aluminum_extrusion_face.stl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]
2025-11-17 fixed frame part
    [aluminum_extrusion.STL]
2025-11-17 fix frame piece
    [aluminum_extrusion.STL]
2025-11-17 fixed bom
2025-11-17 refixed bom
2025-11-17 Clarify Control Unit power connection in PU documentation
    Updated the description of the Control Unit power connection to specify 'to mini USB'.
2025-11-17 adding flow chart part 1
2025-11-17 Updated power info
2025-11-18 Updated to GaN FET
2025-11-18 Reverted back to MOSFET
2025-11-18 Updated to Raspberry Pi 5
2025-11-18 Added level converter and Buildable Schematic
2025-11-18 Fixed Buildable Schematic (5V for Electromagnet)
2025-11-18 Update Detailed Design.md
    BOM update #1
2025-11-18 Update Detailed Design.md
    updated the BOM and some of the paragraphs
2025-11-20 Fixed level converter and stepper motor interfaces
2025-11-21 Update Detailed Design.md
    Update the BOM
2025-11-21 Create Power_Budget.md
    1st for the power budget
2025-11-21 Update Power_Budget.md
    Cleaning it up a bit...
2025-11-21 Update Power_Budget.md
    Added the Wall charger
2025-11-21 Create Power_Tree.md
    create the power tree
2025-11-21 Update Power_Tree.md
    formatting...
2025-11-21 Update Power_Budget.md
    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
2025-11-21 Update Power_Tree.md
    Formatting.....................
2025-11-21 Added driver code libraries
2025-11-22 Update flowchart image in Detailed Design document
2025-11-22 Revise design document for electrical and thermal aspects
    Updated sections on electrical and thermal considerations, added details about the Raspberry Pi 5 Active Cooler, and revised the total cost of components.
2025-11-24 Added Arduino pinout diagram
2025-11-24 Change buildable schematic image to Buildable_for_PU2.png
    Updated the image for the buildable schematic in the documentation.
2025-11-24 Fixed component housing
2025-11-26 updated BOM, added schematics
2025-12-01 removing old 3D models
    [2018_CableCarriers_1.stl, 2020_aluminum_extrusion.STL, 2020_aluminum_extrusion_face.stl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]
2025-12-01 adding individual custom parts
    [Electromagnet_Support.stl, Electronic_Support_A.stl, Electronic_Support_B.stl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]
2025-12-01 Update Power_Tree.md
    updated the power tree
2025-12-01 Update Power_Budget.md
    dido
2025-12-02 redo bom
2025-12-02 clarification on cad model dimensions
2025-12-02 adding cable models
    [CableChain.stl, CableChainEnds.stl]
2025-12-02 add cable chain to detail
2025-12-02 Added the Power_Tree Diagram
2025-12-02 Add specifications, cad drawings, update function
2025-12-02 Add buildable electrical schematic
2025-12-03 update stepper schematic and made interfaces a bit better
2025-12-03 fixing electrical schematic
2025-12-03 Added BOM and Analysis
2026-01-23 Update Detailed_Design_PSU.md
    Update with new batteries.
    -- BOM
    -- analysis
    -- references
    -- Tree
    -- Budget
    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
2026-02-03 Noticed extra resistor (copied) in BOM
2026-02-03 Changed MOSFET product to account for perfboard
2026-02-04 Update Detailed_Design_PU.md
    changed bom due to price spike
2026-02-04 Update Detailed_Design_PSU.md
    clarification on the battery connectors.
2026-02-04 fix bom links
2026-02-13 Update Detailed_Design_PSU.md
    Fix da BOM
2026-02-13 Update Power_Budget.md
    Update Power_Budget
2026-02-13 Update Power_Tree.md
    Update Power_Tree
2026-02-16 Updated bom (NO MORE HOME DEPOT!!!)
2026-03-25 Update Power_Tree.md
    moved the placement of the stepper driver boards
2026-03-25 Update Detailed_Design_PSU.md
    update the power tree 2 the detailed design
2026-04-21 Update BOM
2026-05-05 adding post detailed design parts and organizing
    [CableChain.stl, CableChainEnds.stl, Electromagnet_Support.stl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]
2026-05-05 Add chess board CAD files
    [Automated Chess Board.stl, Chess Pieces.stl]
2026-05-06 Allison did this :D
    [INN_Topology.dwg]
2026-05-06 Rename Documentation/Instruction Manual/Wire_Pins_Diagram.jpg to Documentation/Instruction Manual/Images/Wire_Pins_Diagram.jpg
2026-05-06 Finished Instruction Manual! Email nomacphers42@tntech.edu if you have more questions!! (or nathan@mac-fam.net if I die)
